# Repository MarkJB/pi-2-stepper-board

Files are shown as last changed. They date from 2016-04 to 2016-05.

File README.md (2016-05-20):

Copyright 2016 Mark Benson. Portions probably copyright Raspberry Pi foundation (https://github.com/raspberrypi/hats) (Specifically the HAT Spec I2C EEPROM & Back-feed circuits) so I'm not attempting to assert any Copyright over them, besides my work is licensed under Creative Commons so not sure what else I can do. I'm not a lawyer... thinking about this stuff makes my brain ache.

License: CC-BY 4.0

No warranty implied or given. Use at your own risk.

Repo branches:

Master is at v1.01b

PCBs in the wild (4) at v1.0b

* v1.0a - Pi 2/3 add-on board. Original version.
* v1.0b - Pi 2/3 HAT spec capable board. PCB follows the Pi Foundation HAT spec https://github.com/raspberrypi/hats
* v1.01b - Fixes - Swapped com port pins (Pi Tx/Rx now nearest GPIO and Arduino Tx/Rx nearest Arduino as that seems more logical) - Changed LED for Bi-colour LED, uses existing LED GPIO Pin 7 (GP4) and adds Pin 17 (GP17) - Removed plating from NTPH camera slot - Fixed front silk screen Endstop2 graphic line now points to P3.
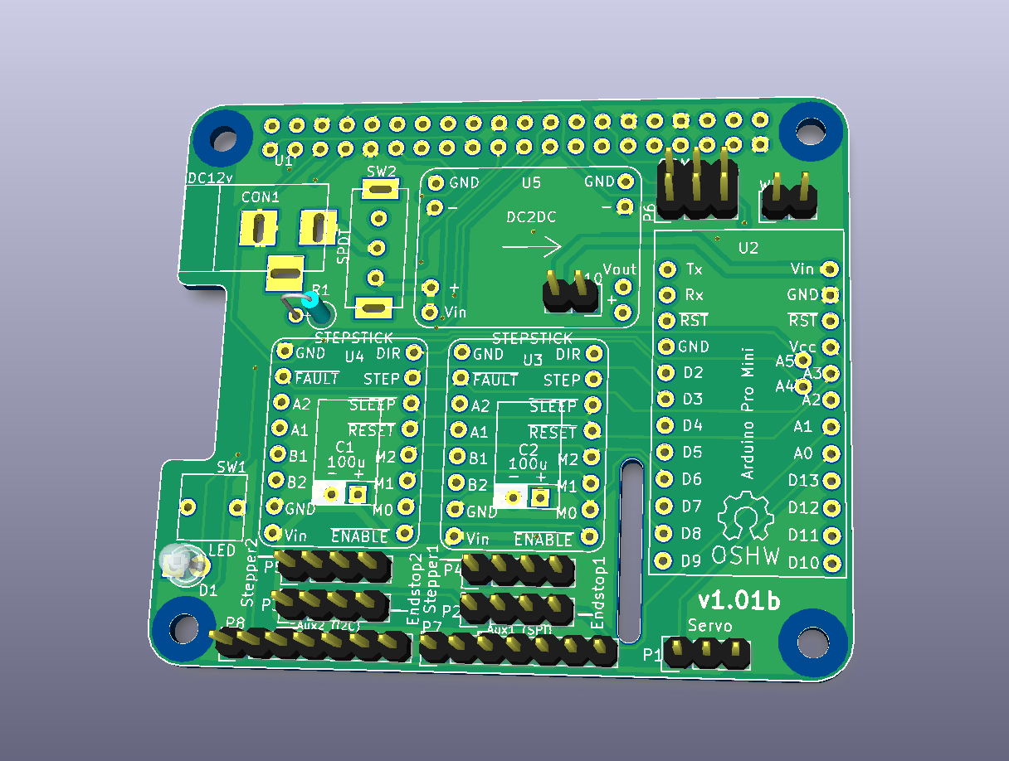
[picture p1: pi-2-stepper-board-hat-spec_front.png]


###This is my Pi 'HAT'* drawing machine add-on board for the Raspberry Pi 2 (and later).

It can drive 2 stepper motors and a servo, has provision for end stop switches and both I2C and SPI peripherals.

Designed for use with vPiP (https://github.com/brianinnes/vpip). vPiP is a Python based vertical hanging plotter control software.

This board is a work in progress and is currently untested.

vPiP is as yet unreleased. More information as it becomes available.

I wouldn't bother making one yet...

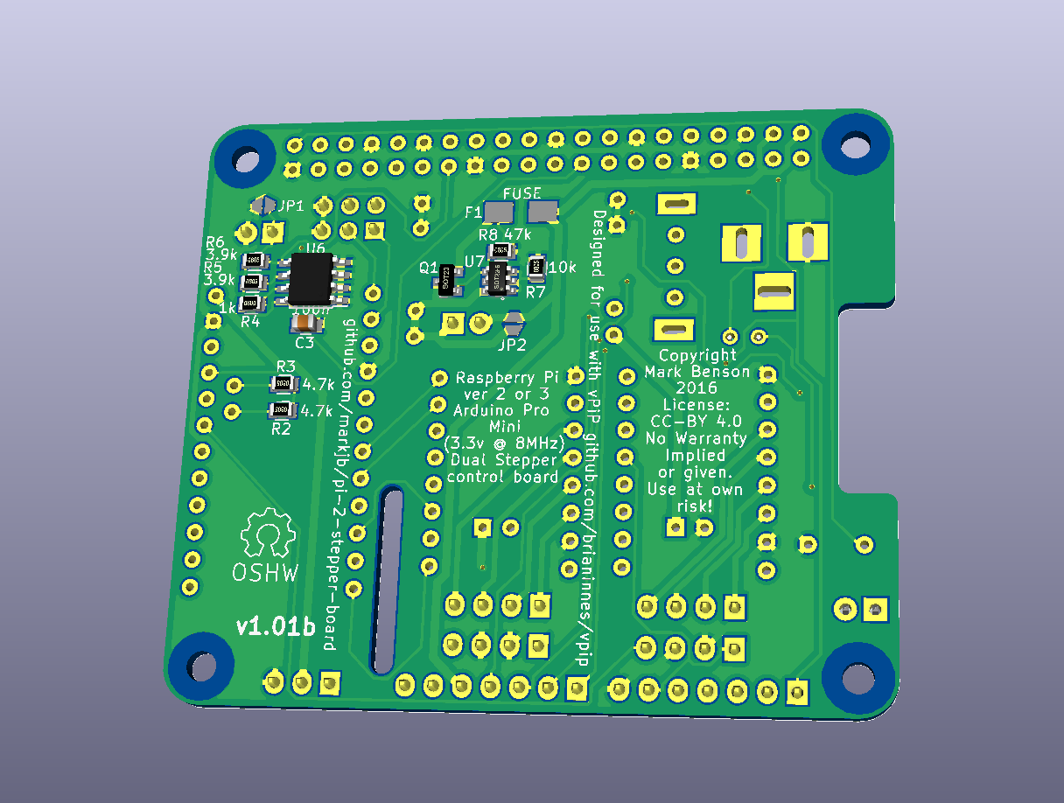
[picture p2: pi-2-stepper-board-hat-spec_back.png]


\* 'HAT' because while the board supports the HAT spec, it would have to be assembled with the HAT spec components (the EEPROM would need to be programmed, plus a few other pyhsical additions like a specific height GPIO connector and stand-offs) to be considered a HAT without any reservations.

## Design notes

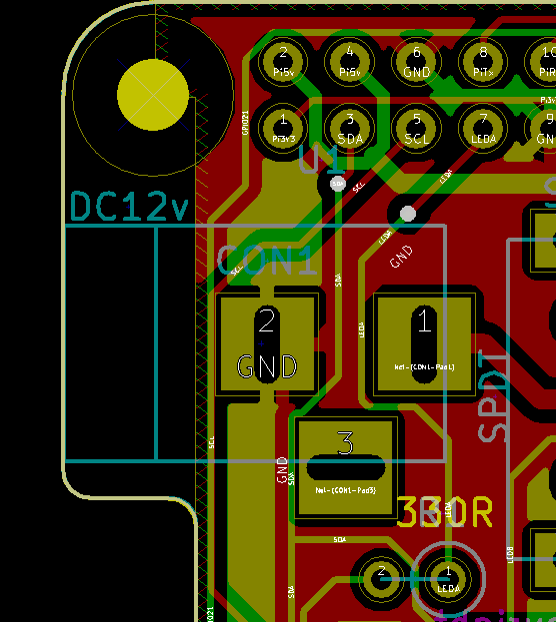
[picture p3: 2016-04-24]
wifi_antenna_no_copper.png

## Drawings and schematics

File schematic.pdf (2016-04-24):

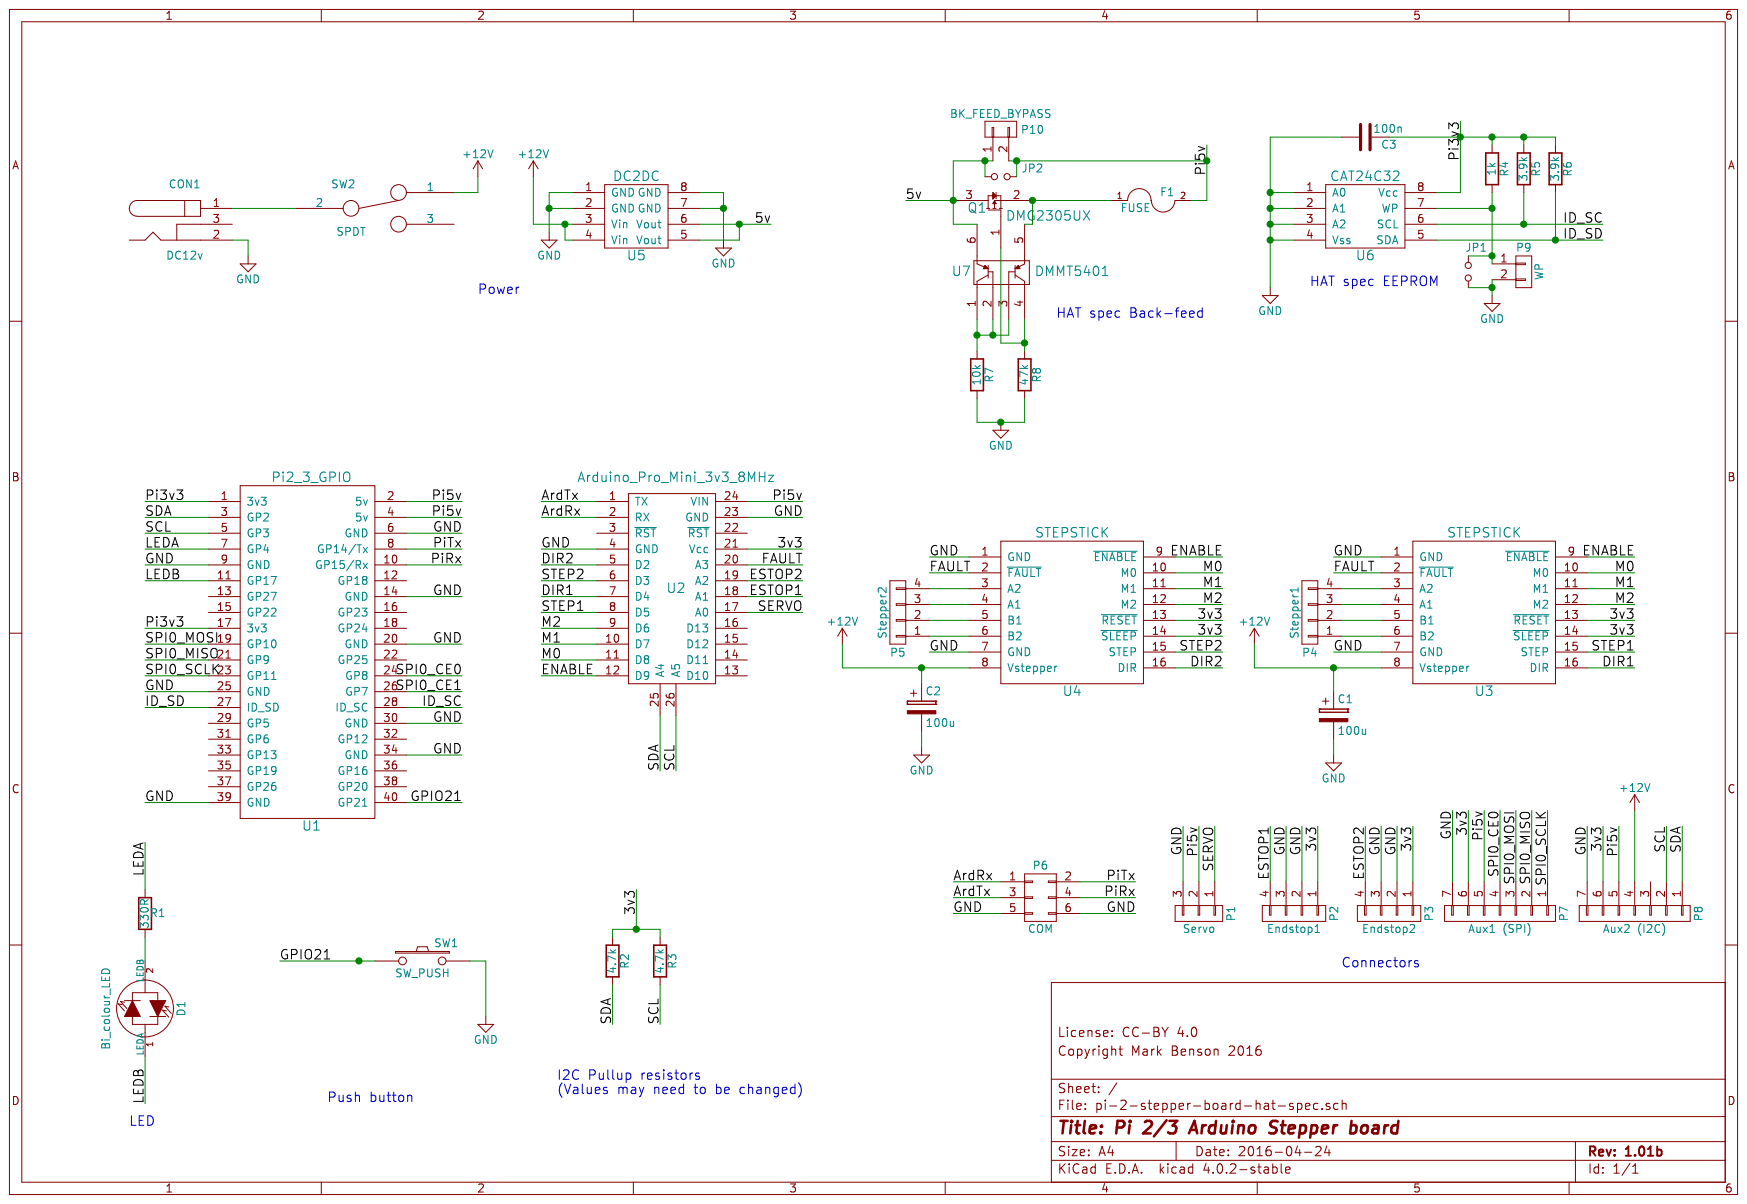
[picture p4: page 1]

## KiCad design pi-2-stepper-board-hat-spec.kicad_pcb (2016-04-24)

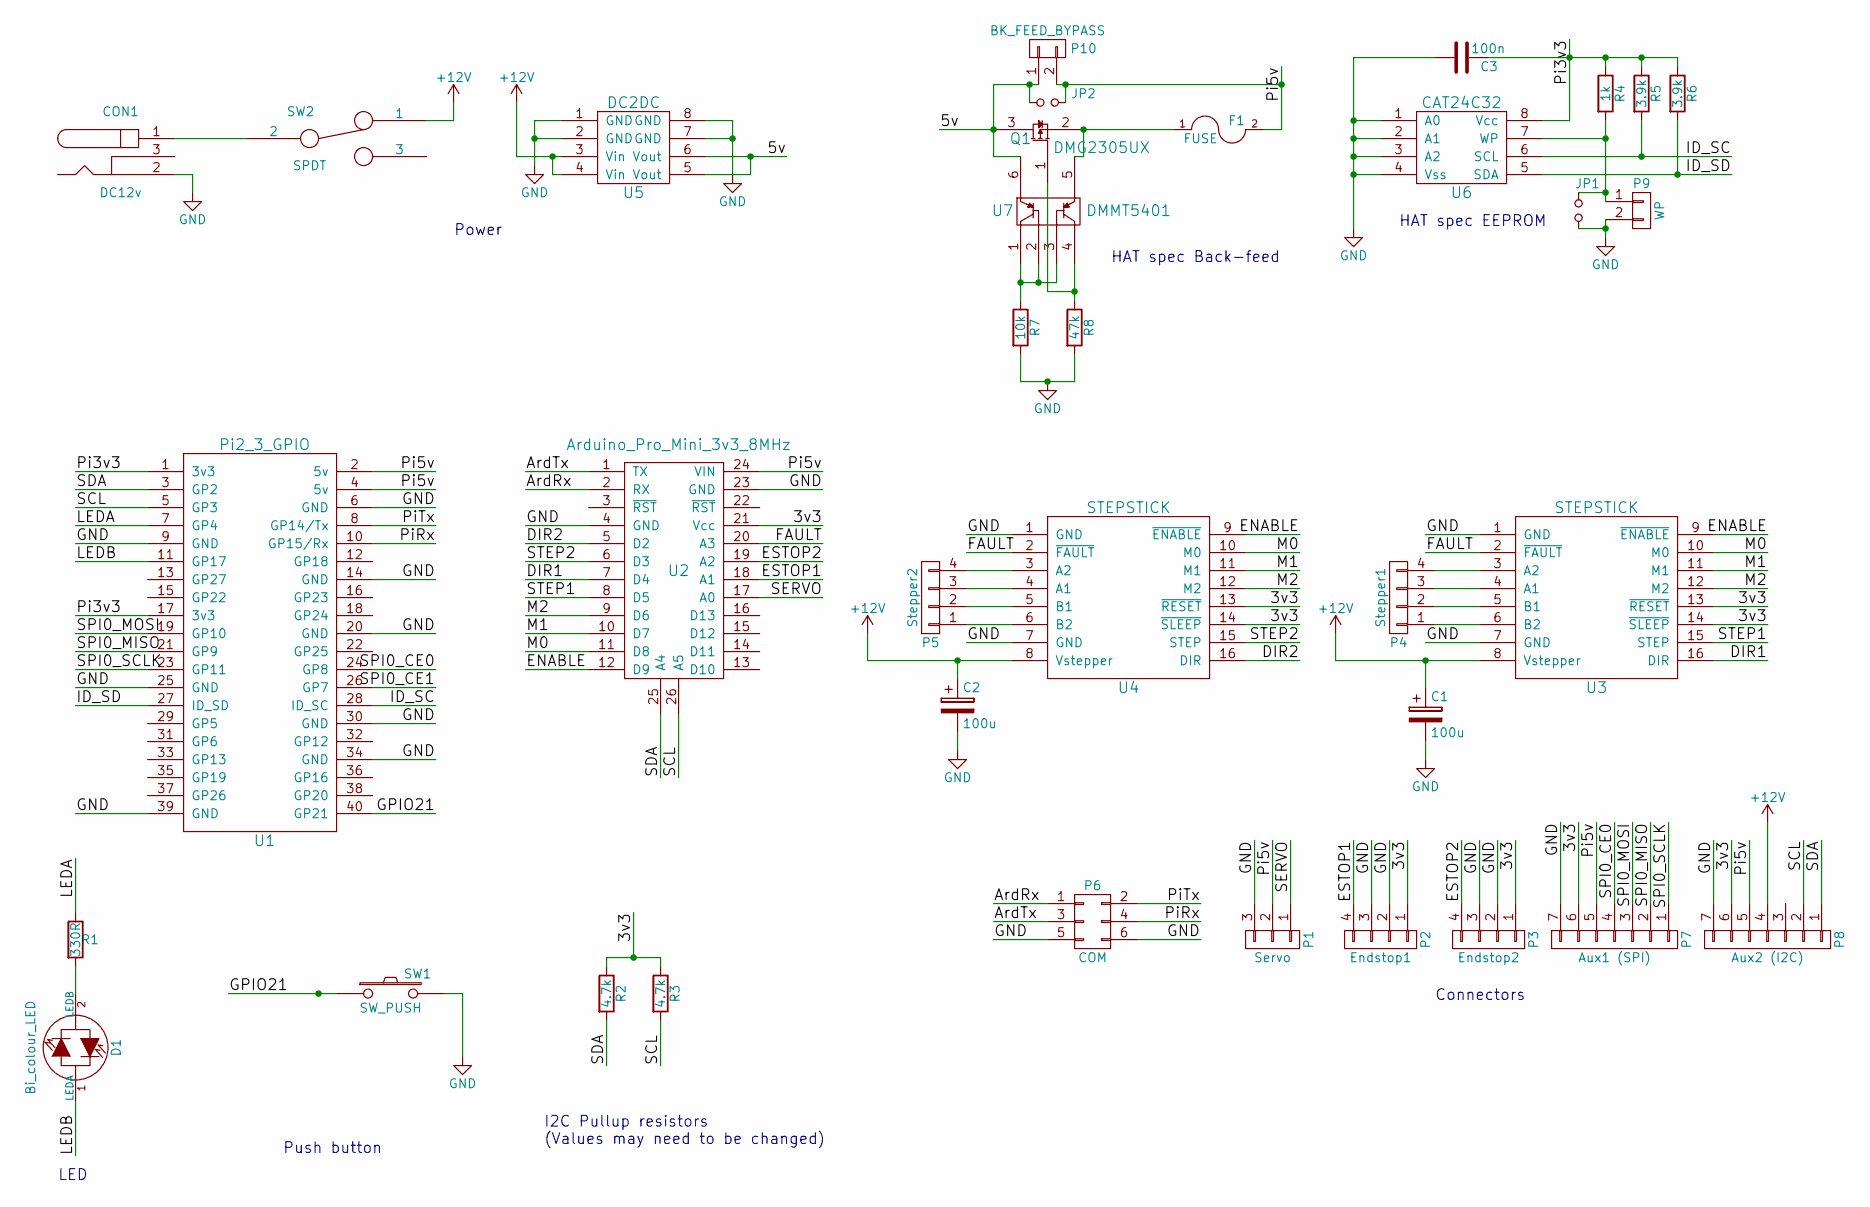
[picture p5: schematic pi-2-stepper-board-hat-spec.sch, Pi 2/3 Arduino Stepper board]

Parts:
C1, C2: 100u; Cap_laying_flat_2.5mm_lead_pitch
C3: 100n; C_0805
CON1: DC12v; BARREL_JACK
D1: Bi_colour_LED; LED-3MM
F1: FUSE; Fuse_SMD1206_HandSoldering
JP1, JP2: Jumper_NO_Small; Solder_Jumper
P1: Servo; Pin_Header_Straight_1x03
P2: Endstop1; Pin_Header_Straight_1x04
P3: Endstop2; Pin_Header_Straight_1x04
P4: Stepper1; Pin_Header_Straight_1x04
P5: Stepper2; Pin_Header_Straight_1x04
P6: COM; Pin_Header_Straight_2x03
P7: Aux1 (SPI); Pin_Header_Straight_1x07
P8: Aux2 (I2C); Pin_Header_Straight_1x07
P9: WP; Pin_Header_Straight_1x02
P10: BK_FEED_BYPASS; Pin_Header_Straight_1x02
Q1: DMG2305UX; SOT-23
R1: 330R; R1
R2, R3: 4.7k; R_0805
R4: 1k; R_0805
R5, R6: 3.9k; R_0805
R7: 10k; R_0805
R8: 47k; R_0805
SW1: SW_PUSH; TactSw
SW2: SPDT; SlideSw
U1: Pi2_3_GPIO; Pi_2_3_Hat_spec
U2: Arduino_Pro_Mini_3v3_8MHz; Arduino_Pro_Mini
U3, U4: STEPSTICK; Stepstick
U5: DC2DC; DSUN_DC2DC
U6: CAT24C32; SOIC-8_3.9x4.9mm_Pitch1.27mm
U7: DMMT5401; SOT-23-6

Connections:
+12V: C1.1, C2.1, P8.4, SW2.1, U3.8 (Vstepper), U4.8 (Vstepper), U5.3 (Vin), U5.4 (Vin)
/3v3: P2.1, P3.1, P7.6, P8.6, R2.1, R3.1, U2.21 (Vcc), U3.13 (~RESET), U3.14 (~SLEEP), U4.13 (~RESET), U4.14 (~SLEEP)
/ArdRx: P6.1, U2.2 (RX)
/ArdTx: P6.3, U2.1 (TX)
/DIR1: U2.7 (D4), U3.16 (DIR)
/DIR2: U2.5 (D2), U4.16 (DIR)
/ENABLE: U2.12 (D9), U3.9 (~ENABLE), U4.9 (~ENABLE)
/ESTOP1: P2.4, U2.18 (A1)
/ESTOP2: P3.4, U2.19 (A2)
/FAULT: U2.20 (A3), U3.2 (~FAULT), U4.2 (~FAULT)
/GPIO21: SW1.1, U1.40 (GP21)
/ID_SC: R5.2, U1.28 (ID_SC), U6.6 (SCL)
/ID_SD: R6.2, U1.27 (ID_SD), U6.5 (SDA)
/LEDA: R1.1, U1.7 (GP4)
/LEDB: D1.1 (LEDA), U1.11 (GP17)
/M0: U2.11 (D8), U3.10 (M0), U4.10 (M0)
/M1: U2.10 (D7), U3.11 (M1), U4.11 (M1)
/M2: U2.9 (D6), U3.12 (M2), U4.12 (M2)
/Pi3v3: C3.1, R4.1, R5.1, R6.1, U1.1 (3v3), U1.17 (3v3), U6.8 (Vcc)
/Pi5v: F1.2, JP2.2, P1.2, P7.5, P8.5, P10.2, U1.2 (5v), U1.4 (5v), U2.24 (VIN)
/PiRx: P6.4, U1.10 (GP15/Rx)
/PiTx: P6.2, U1.8 (GP14/Tx)
/SCL: P8.2, R3.2, U1.5 (GP3), U2.26 (A5)
/SDA: P8.1, R2.2, U1.3 (GP2), U2.25 (A4)
/SERVO: P1.1, U2.17 (A0)
/SPI0_CE0: P7.4, U1.24 (GP8)
/SPI0_CE1: U1.26 (GP7)
/SPI0_MISO: P7.2, U1.21 (GP9)
/SPI0_MOSI: P7.3, U1.19 (GP10)
/SPI0_SCLK: P7.1, U1.23 (GP11)
/STEP1: U2.8 (D5), U3.15 (STEP)
/STEP2: U2.6 (D3), U4.15 (STEP)
unnamed: CON1.1, SW2.2
unnamed: D1.2 (LEDB), R1.2
unnamed: F1.1, Q1.2, U7.5
unnamed: JP1.1, P9.1, R4.2, U6.7 (WP)
unnamed: P4.1, U3.6 (B2)
unnamed: P4.2, U3.5 (B1)
unnamed: P4.3, U3.4 (A1)
unnamed: P4.4, U3.3 (A2)
unnamed: P5.1, U4.6 (B2)
unnamed: P5.2, U4.5 (B1)
unnamed: P5.3, U4.4 (A1)
unnamed: P5.4, U4.3 (A2)
unnamed: Q1.1, R8.1, U7.4
unnamed: R7.1, U7.1, U7.2, U7.3

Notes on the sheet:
Push button
I2C Pullup resistors (Values may need to be changed)
Power
Connectors
HAT spec EEPROM
LED
HAT spec Back-feed

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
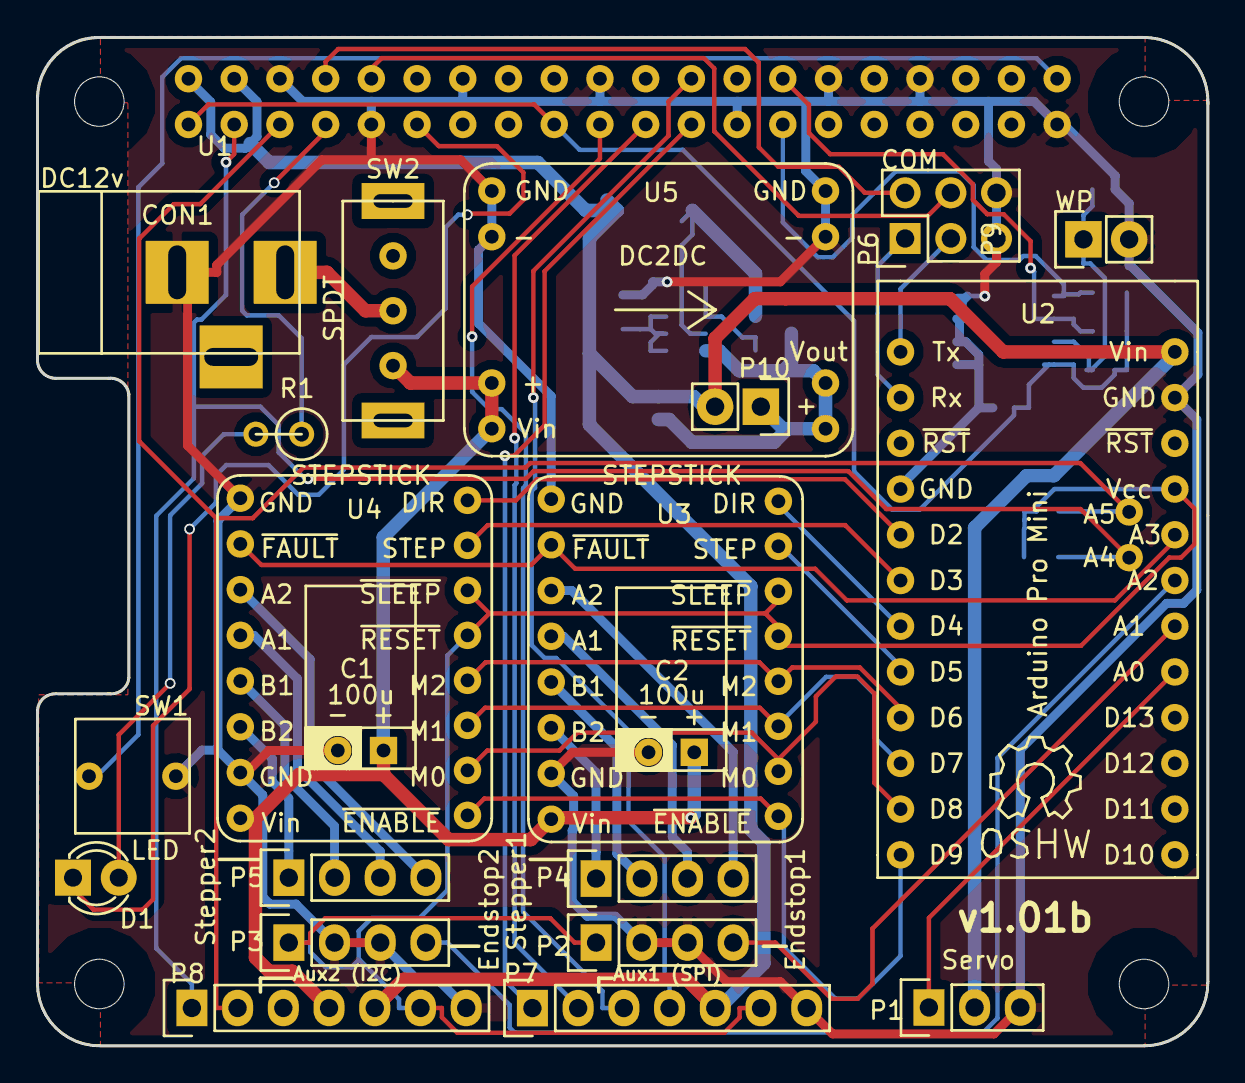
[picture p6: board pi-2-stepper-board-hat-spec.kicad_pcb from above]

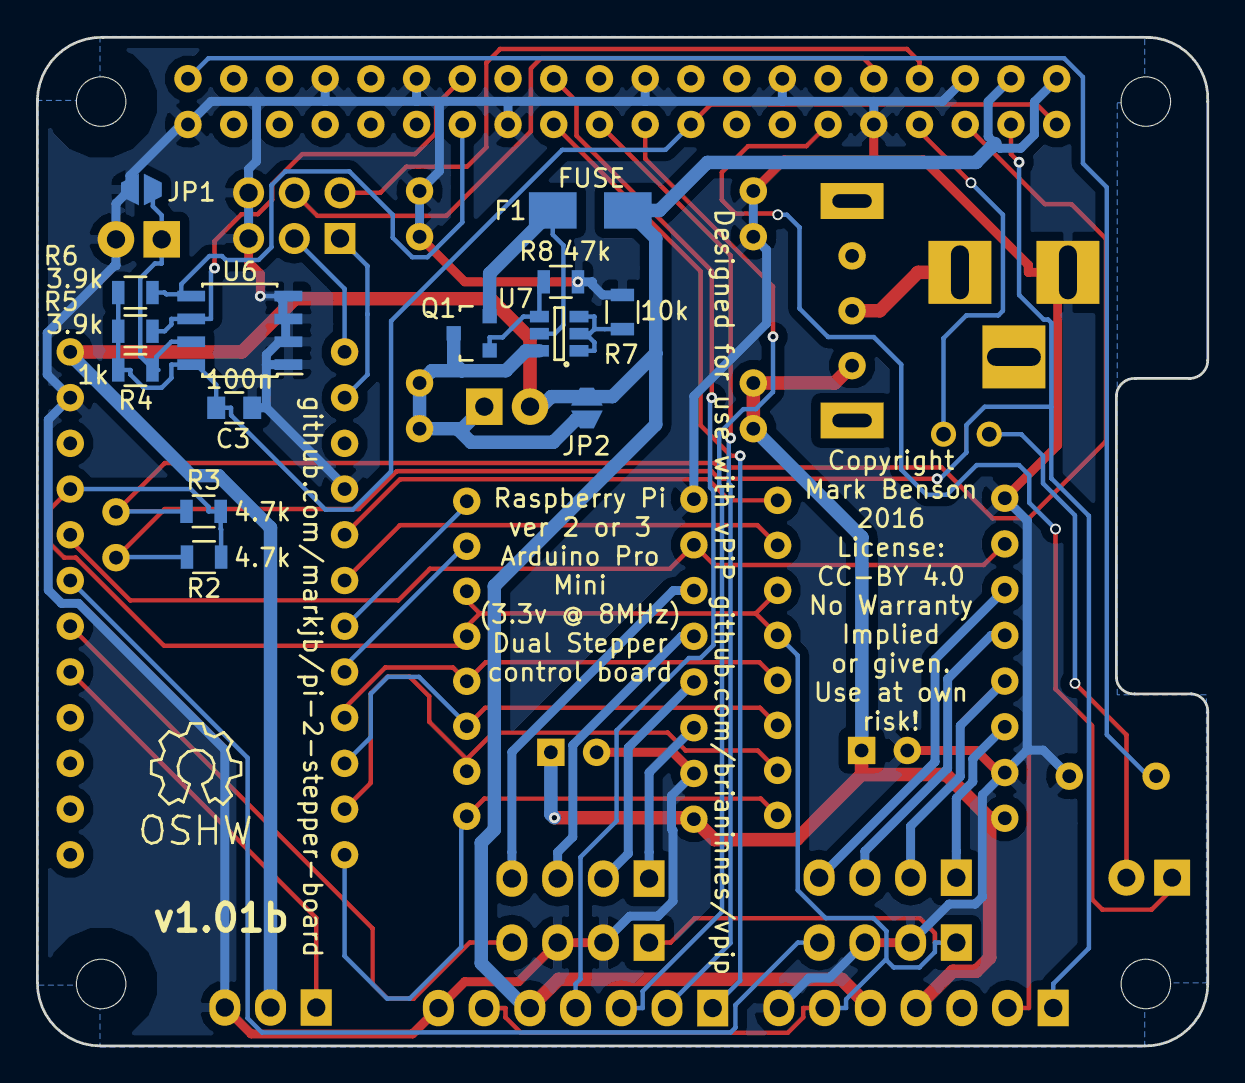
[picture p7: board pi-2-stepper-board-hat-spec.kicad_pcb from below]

Board: 2 copper layers, 65.0 x 56.0 mm, 36 parts (14 on the bottom side), 47 nets.

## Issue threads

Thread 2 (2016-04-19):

Camera slot is plated. Should be unplated.

MarkJB, 2016-04-19:
The hole for the Pi camera cable came back from the PCB manufacturers plated.

It should be un-plated. It isn't a big deal as it is electrically isolated but would be better un-plated.

Check designs and amend as required.

MarkJB, 2016-04-24:
Set the 'Layers - Copper' association to 'None'.

Was set to 'All copper layers'.

I think that is why the hole ended up plated even though it is a 'NPTH, Mechanical' hole in KiCAD.

MarkJB, 2016-04-24:
Scratch that... it won't allow a hole that doesn't exist on one or more copper layers. It then shows a warning to the effect that if you want hole with no plating, make them drill size=pad size (i.e. no clearance for pad and plating).

MarkJB, 2016-04-24:
Fixed in commit #7

Closed 2016-04-24.

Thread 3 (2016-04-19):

Change 3mm LED to be bi-colour

MarkJB, 2016-04-19:
The GPIO controlled LED could be much more useful as a status indicator if it was a bi-colour led. Would require an additional GPIO be routed to the LED.

MarkJB, 2016-04-24:
Fixed in commit #7

Closed 2016-04-24.

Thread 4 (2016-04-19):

Error on top silkscreen - Endstop2 points to P5 (Stepper2)

MarkJB, 2016-04-19:
Error on top silkscreen - Endstop2 points to P5 (Stepper2)

MarkJB, 2016-04-24:
Fixed in commit #7

Closed 2016-04-24.

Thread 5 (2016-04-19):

Com port header pins are upside down

MarkJB, 2016-04-19:
Not necessrily an issue, but logically I'd expect the Arduino side to be nearest the Ardiuino and vice-versa.

The Arduino tx/rx pins are nearest the GPIO and the Pi tx/rx pins are nearest the Arduino.

MarkJB, 2016-04-21:
Leave connector where it is. Don't turn it around otherwise the ground pins will be on the wrong side between versions. Better to swap pin assignments in the schematic and re route the connections so they are on the logical side of the connector.

MarkJB, 2016-04-24:
#7

MarkJB, 2016-04-24:
Fixed in commit #7

Closed 2016-04-24.

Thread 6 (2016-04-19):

Have to reset Arduino to get things working

MarkJB, 2016-04-19:
When I run vPiP (python test1.py) the program sits at Polargraph __exit__ until I reset the Arduino at which point the servo does its down-up-down move and then the steppers work...

Perhaps the original program is expecting the Arduino to reset upon connect. I don't think the Pro Minis do that as they don't have the USB serial port reset on connect feature that some Arduinos seem to have.

Maybe the firmware isn't sending a 'hello' type command except at reset?

brianinnes, 2016-04-19:
The only thing done with the serial port in the setup routine of the Arduino code is :
```
  Serial.begin(57600);
  Serial.setTimeout(0);
```

There are a few GPIO pin setup commands then the servo code config runs :
```
  penUpServo.attach(PENUP_SERVO_PIN);
  penUpServo.write(PENUP_ANGLE);
  delay(1000);
  penUpServo.write(PENDOWN_ANGLE);
  delay(1000);
  penUpServo.write(PENUP_ANGLE);
```

so the servo should cycle at power up before any serial comms takes place.

MarkJB, 2016-04-20:
I've been trying to track the issue down.

I've managed to get the Arduino IDE running on the Pi and am able to program the Pro Mini directly over the GPIO. I have to reset the Arduino the instant the IDE says 'Uploading' for it to work but that is normal for a Pro Mini.

I uploaded a serial echo program and was able to see chars echoed to the Arduino and back via minicom on the Pi.

I reuploaded the stepper firmware and the servo did its up-down-up move.

I tried running python test1.py but it hangs until I reset the pro mini which is why I was thinking the serial comms is out of sync or not doing a 'hello' type command.

I shutdown, powered off and powered on the whole thing and sure enough the servo did its up-down-up move. But python test1.py still hangs until I reset the Arduino.

MarkJB, 2016-04-21:
I left it sitting to see if the serial comms would timeout and start running but it didn't.

MarkJB, 2016-04-23:
Added some debugging on the Arduino serial coms and it does appear to be timing out and requesting more data, but vPiP isn't hearing or responding to it, or is out of sync.

I can watch the moveDataRequestPending value being set to 128 when requestMoreSerialData() is run.

It then decrements as if data is being read.

The data being read is 'ó' (ASCII 224).

When moveDataRequestPending reaches 0 the Arduino asks for more data and it carries on like that but nothing useful happens (motors don't move).

Brian, I'm punting this across to vPiP for you to have a look at when you have a board up and running.

Closed 2016-04-23.

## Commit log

2016-03-16 Added I2C updated text
    [pi-2-stepper-board.kicad_pcb, pi-2-stepper-board.sch]
2016-03-28 Added I2C port and other fixes
    [pi-2-stepper-board.kicad_pcb, pi-2-stepper-board.sch]
2016-04-06 Design to HAT spec
    Added HAT spec board (Cable cut-outs, EEPROM, Back-feed circuit). Added
    jumpers to by-pass back-feed circuit. Fixed NPTH pads. Added LED.
    Removed push button pull-up resistor.
    NOTE: If HAT spec back-feed circuit is not fitted, Pi & Arduino are not
    powered by the DC-DC converter until either P10 or JP2 are shorted. This
    also by-passes the Poly fuse F1. Here be dragons...
    [pi-2-stepper-board-hat-spec-B.Cu.gbl, pi-2-stepper-board-hat-spec-B.Mask.gbs, pi-2-stepper-board-hat-spec-B.SilkS.gbo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]
2016-04-06 Added version number v1.0b
    [pi-2-stepper-board-hat-spec-B.Cu.gbl, pi-2-stepper-board-hat-spec-B.Mask.gbs, pi-2-stepper-board-hat-spec-B.SilkS.gbo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]
2016-04-07 Update licence version
    [pi-2-stepper-board-hat-spec.kicad_pcb]
2016-04-07 Clean up repo - board 1.0b hat spec
    [pi-2-stepper-board.kicad_pcb, pi-2-stepper-board.sch]
2016-04-07 Clean up repo
    [pi-2-stepper-board.kicad_pcb, pi-2-stepper-board.sch]
2016-04-24 Milestone 1.01b fixes
    Swapped com port sides
    Replaced LED with Bi-colour LED
    Fixed Silkscreen & NPTH plated slot
    [pi-2-stepper-board-hat-spec.kicad_pcb, pi-2-stepper-board-hat-spec.sch]
2016-04-24 Clean up schematic
    [pi-2-stepper-board-hat-spec.sch]
2016-04-24 Update License version
    Trying to get all the mentions of the CC-BY license to say CC-BY 4.0 as
    that is the intended license and some of the files are still a bit
    messy.
    [pi-2-stepper-board-hat-spec.sch]
2016-04-24 Updated another instance of an incorrect license
    [pi-2-stepper-board-hat-spec.kicad_pcb]

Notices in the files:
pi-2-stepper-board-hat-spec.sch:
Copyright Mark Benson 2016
